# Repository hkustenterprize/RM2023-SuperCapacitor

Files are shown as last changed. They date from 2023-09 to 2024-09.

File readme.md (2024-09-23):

<div align='left'>
    <h1> 本项目续作已开源 </h1>
</div>

请参考
|||
|-|-|
|论坛|[【RM2024超级电容控制器完全开源】 (史上最详细的开源！)香港科技大学ENTERPRIZE战队](https://bbs.robomaster.com/article/54127)|
|GitHub|[hkustenterprize/RM2024-SuperCapacitorController](https://github.com/hkustenterprize/RM2024-SuperCapacitorController)|

<div align='center'>
    <h1>廉价，可靠，高效</h1>
</div>

<div align='center'>
    <h2>RM2023香港科技大学ENTERPRIZE</h2>
</div>

<div align='center'>
    <h1>数控超级电容方案开源</h1>
</div>

> 设计者：蒋益诚
>
> 文档撰写：蒋益诚  戎羿
>
> 香港科技大学ENTERPRIZE战队

# 前言

在RoboMaster机甲大师赛事中，严苛的底盘功率限制规则迫使各参赛队伍从软件和硬件方面研究高效的底盘功率管理方案。早在2018年末，大连交通大学TOE战队，桂林电子科技大学Evolution战队与香港科技大学ENTERPRIZE战队等便相继开源了各具特色的超级电容方案。2020年，官方裁判系统超级电容管理模块与相关限制规则加入，超级电容的使用更加规范化，给各战队带来了不小的挑战。

2021赛季末大连理工凌_BUG战队开源了他们基于双向BUCK-BOOST电路构建的超级电容控制模块，引发广泛关注。我队取其精华，在其基础上进行数次迭代，历经一年时间，完成了低成本，稳定可靠，大功率，高效率的数控超级电容方案。本着技术交流和初心高于胜负的初衷我队现决定将此方案开源，欢迎大家交流学习。

# 方案回顾

自2018年超级电容方案诞生以来，其大致电路方案可分为以下3种

1. 电源 $\Rightarrow$ 恒功率充电模块 $\Rightarrow$ 超级电容 $\Vert$ 底盘电机
2. 电源 $\Rightarrow$ 恒功率充电模块 $\Rightarrow$ 超级电容 $\Rightarrow$ 恒压放电模块 $\Leftrightarrow$ 底盘电机
3. 电源 $\Vert$ 底盘电机 $\Leftrightarrow$ 双向可控功率模块 $\Leftrightarrow$ 超级电容

笔者将基于自身理解对这些方案进行简单优缺点分析

## 电源  $\Rightarrow$  恒功率充电模块  $\Rightarrow$  超级电容 $\Vert$ 底盘电机

本方案直接明了，通过恒功率充电模块对整个底盘的输入功率进行控制，并通过超级电容对能量进行缓存。

该方案主要有以下几个优点：

1. 超级电容直接和底盘电机并联，相当于自带了高效的动能回收机制
2. 理想状态下能够保证在任何时候都无法超功率

在充放电的过程中，底盘电机母线电压是随超级电容电压的波动而波动的，因此该方案存在以下几个显著缺点

1. 如果电容电量过低，会导致底盘电机欠压保护，或工作不正常
2. 电压不稳定，会影响底盘电机的控制，具体可表现为相同参数下电机的输出力矩，转速等存在较大幅度波动。
3. 动能回收时，会有较大的倒灌电流涌入超级电容组，对电容组及其保护板的设计有一定的考验。
4. 在机器人阵亡后，若电容仍有余电，底盘电机可能仍有足够电压继续移动一段时间，若不做处理可能违反规则
5. 模块之间串联，若有模块损坏或异常断电，则机器人底盘直接掉电，无法继续移动

## 电源 $\Rightarrow$ 恒功率充电模块 $\Rightarrow$ 超级电容 $\Rightarrow$ 恒压放电模块 $\Leftrightarrow$ 底盘电机

该方案在上个方案的基础上增加了一个恒压放电模块，以稳定底盘电机母线电压。

因此，该方案有以下几个优点：

1. 与上个方案一样，理想状态下，底盘不会超功率
2. 在电容电量耗尽前，底盘电机的母线电压相对恒定，能够给电机提供良好的工作环境

由于恒压放电模块可能存在的一些特性，该方案可能存在以下几个缺点：

1. 若恒压放电模块为非同步boost/buckboost或者其控制策略不允许电流倒灌（例如其boost半桥上管采用理想二极管策略控制），则该方案完全无法进行动能回收，且在电机急减速时可能瞬间拉高母线电压，有较大风险烧毁电机
2. 在机器人阵亡后，若电容仍有余电，底盘电机可能仍有足够电压继续移动一段时间，若不做处理可能违反规则
3. 与上个方案一样，模块之间串联，若有模块损坏或异常断电，则机器人底盘直接掉电，无法继续移动。且由于恒压放电模块与底盘电机直接相连，工况较为恶劣，对该模块的设计有较大考验。

## 电源 $\Vert$ 底盘电机 $\Leftrightarrow$ 双向可控功率模块 $\Leftrightarrow$ 超级电容

该方案即为本战队本次开源的方案，灵感源自2021赛季大连理工大学凌BUG战队的开源。

在本方案中底盘电机直接连接到电源，超级电容和一个双向可控功率模块共同构成一个可控的功率补偿系统，凭借高速的功率闭环控制动态对底盘功率进行削峰填谷，从而实现超级电容的能量缓冲。

为便于理解，在此举例。

假设底盘功率限制为60W，电池电压为20V，超级电容处于半充满状态。

若此时底盘电机电流为2A，即底盘电机功率为40W，则双向可控功率模块将使用1A电流对超级电容充电，即充电功率为20W。将多余功率缓存在超级电容中。

若此时底盘电机电流为5A，即底盘电机功率为100W，则双向可控功率模块将使用2A电流对超级电容进行放电，此时放电功率为40W。利用超级电容中的能量补偿底盘功率。

若此时底盘电机电流为-2A，即底盘电机功率为-40W，则双向可控功率模块将使用5A电流对超级电容进行充电，此时充电功率为100W。即动能回收的过程。

该方案具有如下几个主要优点：

1. 并联接入底盘电机母线，即使系统工作异常，只需要及时切断电路（关断MOS管/保险丝熔断等），底盘任可继续正常工作。
2. 无论电容剩余能量如何，底盘电机的母线电压都能保持相对稳定，约等于电源电压，能够给电机提供良好的工作环境。
3. 可以主动限制动能回收的电流，允许部分浪涌电流倒灌回电池，防止损坏超级电容组。
4. 通过简单的代码逻辑，可在底盘电源切断时立即关断系统输出，在机器人阵亡后保存电容能量，同时避免违反规则。

该方案的显著缺点如下：

1. 采用数控方案，对嵌入式程序设计，控制系统设计要求较高，稍有不慎即可能损伤硬件。（我们调试时曾不慎将输出电压升至100V以上）
2. 采用并联方式被动补偿功率，若底盘电控不加以合理限制，仍有超功率风险。

显然，在参赛队伍硬件实力足够的前提下，第三种方案相较于前两种有极大优势。我们本次开源的方案即基于第三种。

# 电学原理

## 升压与降压

首先回顾经典的升压电路与降压电路。为方便理解，假设此处所有DC-DC电路均工作在CCM（连续导通）模式下，MOSFET（场效应管）为理想MOSFET，忽略死区时间， $R_{DSon}$ 等。

- Buck降压。下图左侧为非同步Buck电路，肖特基二极管起到为电感续流的作用。右侧为同步Buck电路，用MOSFET替代了二极管，带来了更低的压降与更灵活的控制。同步Buck电路中，CCM模式下，MOSFET经过**控制**，能够在电流正向的时候导通、反向的时候断开，实现了二极管的功能。

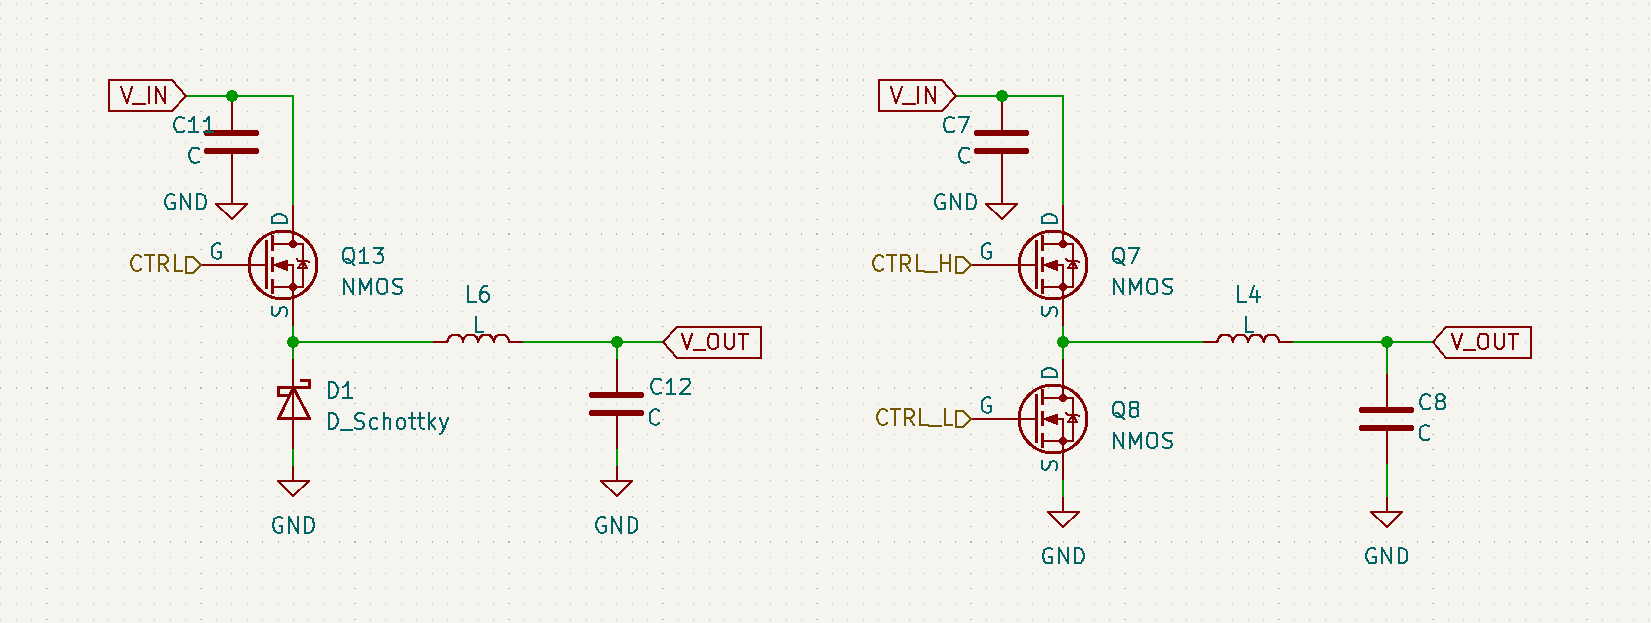
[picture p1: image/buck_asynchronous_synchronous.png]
buck_asynchronous_synchronous
    通过伏秒平衡定律可推导Buck电路在CCM模式下的输入输出电压关系 $\frac{V_{out}}{V_{in}}=D$ ，其中 ${V_{out}}$ 为输出电压， $V_{in}$ 为输入电压， $D$ 为上管导通时间占整个PWM周期的占空比。

- Boost升压。下图左侧为非同步Boost电路，MOSFET对地导通时为电感充能，二极管在此处起到续流和防倒灌作用。右侧为同步Boost电路。用MOSFET替代二极管，在适当的控制下实现了二极管的功能。

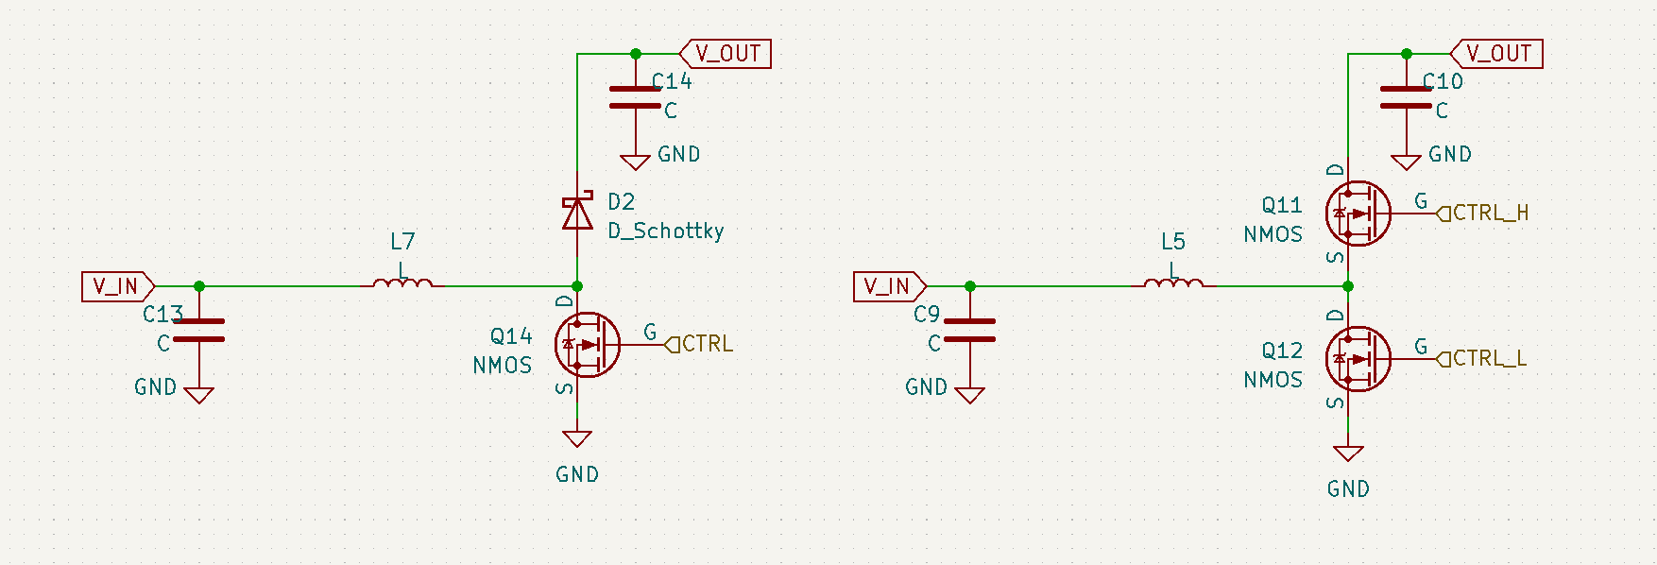
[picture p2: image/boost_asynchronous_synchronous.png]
boost_asynchronous_synchronous
    通过伏秒平衡定律可推导Boost电路在CCM模式下的输入输出电压关系 $\frac{V_{out}}{V_{in}}=\frac{1}{D}$ ，其中 ${V_{out}}$ 为输出电压， $V_{in}$ 为输入电压， $D$ 为上管导通时间占整个PWM周期的占空比（注意是上管）。

  受限于篇幅，在此省略伏秒平衡定律的具体推导过程。

## 双向升降压

同样的，假设一切条件全部理想，将Buck电路的前半段与Boost电路的后半段相连，我们可得到如下的四开关双向Buck-Boost电路。观察可见，此电路为对称结构。

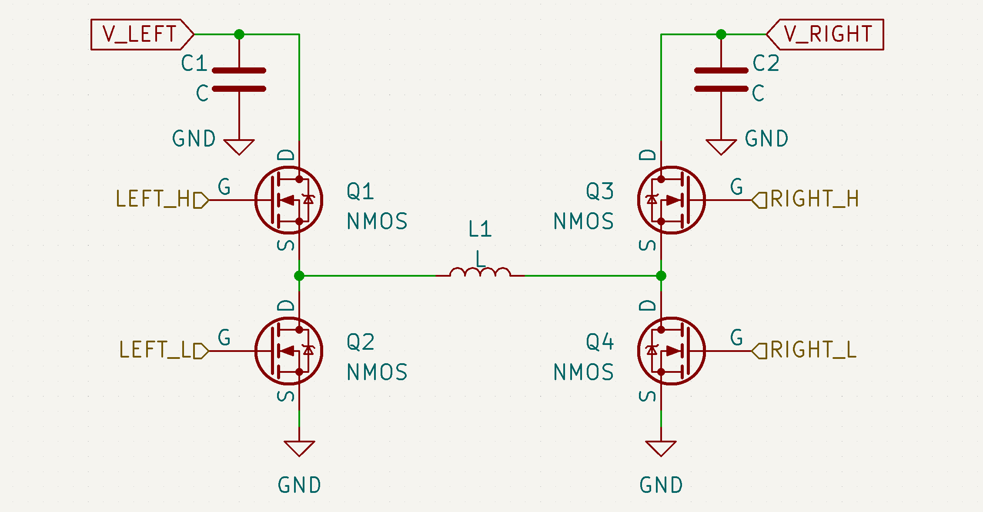
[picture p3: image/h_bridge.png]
image-principle-1


### 假设电流从左往右流动

- 若将RIGHT_H常导通，RIGHT_L常断开，而LEFT_H和LEFT_L继续使用如上的Buck电路控制策略，则等效电路图如下图。这就是完全等效于Buck的拓扑，此时可将电路看作同步Buck，可实现将左侧电降压后提供给右侧。

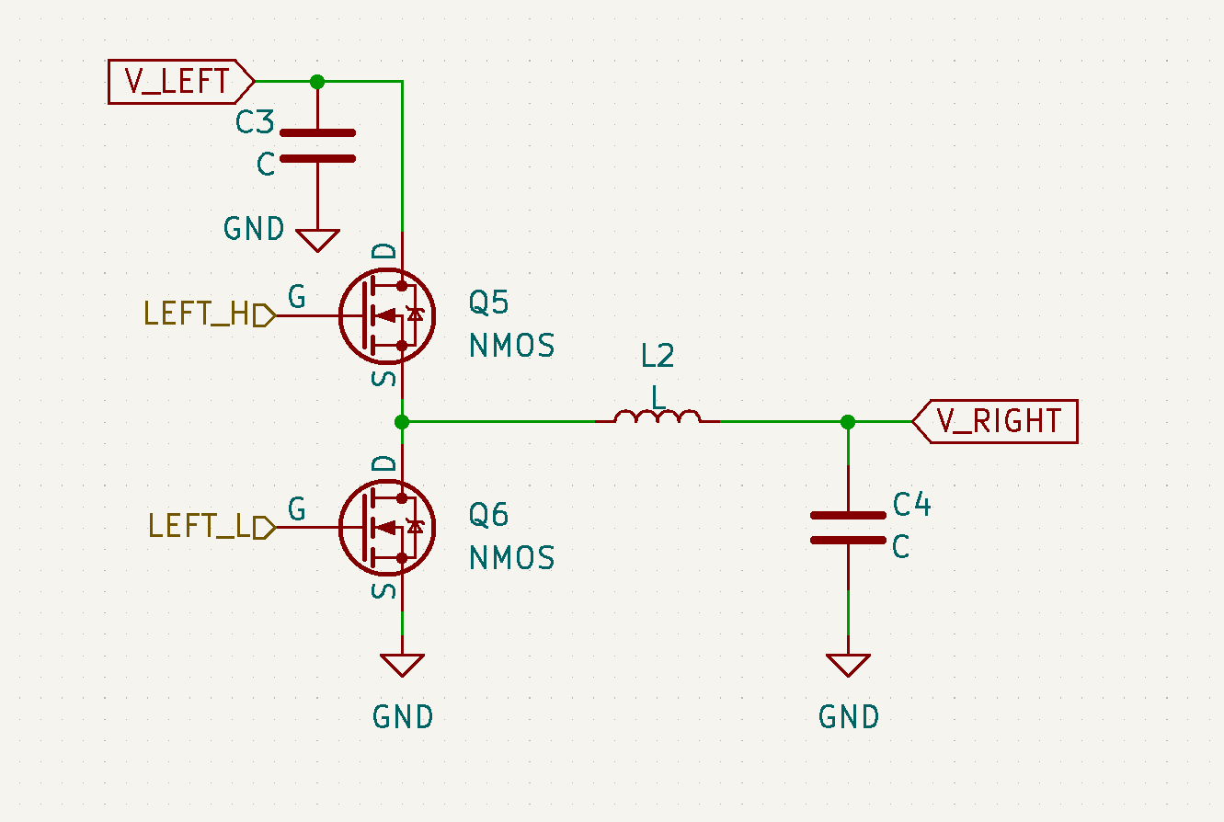
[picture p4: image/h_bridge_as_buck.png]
  
- 若将LEFT_H常导通，LEFT_L常断开，而RIGHT_H和RIGHT_L继续使用如上的Boost电路控制策略，则等效电路如下图。这就是Boost的拓扑，此时将电路看作同步Boost即可实现将左侧电升压后提供给右侧。

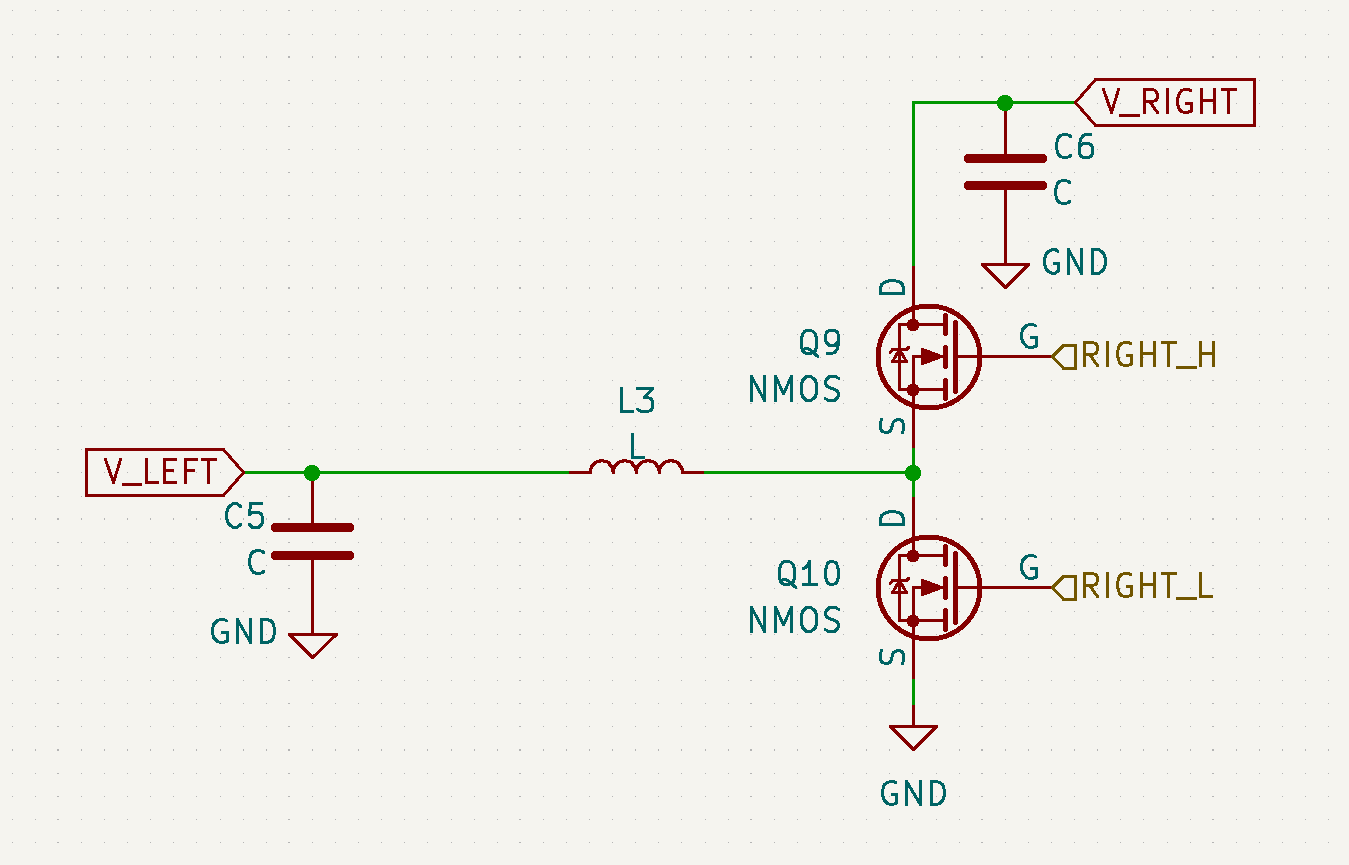
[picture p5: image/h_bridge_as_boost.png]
  
- 第三种情况是需要的左电压与右电压相近。此时实际应用中由于最大占空比以及死区时间等限制，很难单独使用Buck或者Boost拓扑生成所需电压比。于是考虑用Buck控制策略控制左半桥，用Boost控制策略控制右半桥，此即为buck-boost电路。在任意时刻（瞬时），电路可视为Buck电路或Boost电路。（此处省略了一些细节，如为了防止两边的下管同时导通，左右两边的上管占空比应相互制约，同时相位也应错开）此时，无论是使用叠加原理还是通过伏秒平衡定律，我们都可以得到如下结果 $\frac{V_{left}}{V_{right}}=\frac{D_{right}}{D_{left}}$ ，其中， $D_{left}$ 为左侧上管占空比， $D_{right}$ 为右侧上管占空比。

### 假设电流从右往左流动

由于电路完全对称，显然，仅需将Buck与Boost颠倒过来，即可实现与上述完全相同的效果，在此不做过多赘述。

经过同样的推导，我们仍然得到此结果 $\frac{V_{left}}{V_{right}}=\frac{D_{right}}{D_{left}}$ 。

### 总结

在控制这个四开关双向Buck-Boost电路时，实际上**不需要区分电路到底是Buck还是Boost**，也不需要关注电流的流向等，只需给予两个半桥合适的占空比，即可获得想要的左右电压之比。

这种不对电流流向做限制，强制上下管交替导通的控制方式被称为FPWM（强制脉宽调制）模式。由于实现此控制模式的硬件较为简单，本设计采用此控制模式进行控制。

注意：Buck与Boost的互相转换只在 *同步Buck/同步Boost* 中起作用。

## 电流控制

通过以上分析，我们现可构建一个四开关Buck-Boost双向升降压电路。

在RoboMaster以及大多数其他应用场景中。电路中的负载更偏向于阻性，即电压差越大，电流越大，根据这一特点，我们通过控制左右两侧的电压之比进而对左右两侧的平均电流进行控制。

此处举一个例子便于理解。假设左侧为电源，右侧为负载，根据以上分析，我们可推导出右侧电压越大，输出电流越大，右侧电压越小，输出电流越小。此时若输出电流大于目标电流，则我们通过改变左右两侧占空比，控制左右两侧电压之比增大，则右侧电压降低，输出电流也相应减小。若输出电流小于目标电流，则控制占空比减小，右侧电压升高，输出电流增大。当右侧为电压源时，只需反转控制逻辑，即可实现一样的控制效果。在RoboMaster超级电容的应用中，左侧和右侧均可作为负载或电源，当给超级电容充电时，超级电容侧为负载，当超级电容放电时，超级电容侧为电源。

在上述例子中，基于电流反馈控制占空比变化的方式有很多种，在本方案中，我们使用ADC对转换后的电流进行读取，之后使用PID计算所需占空比进行输出，从而实现电流闭环控制。

# 控制模块技术特点

## 实物图

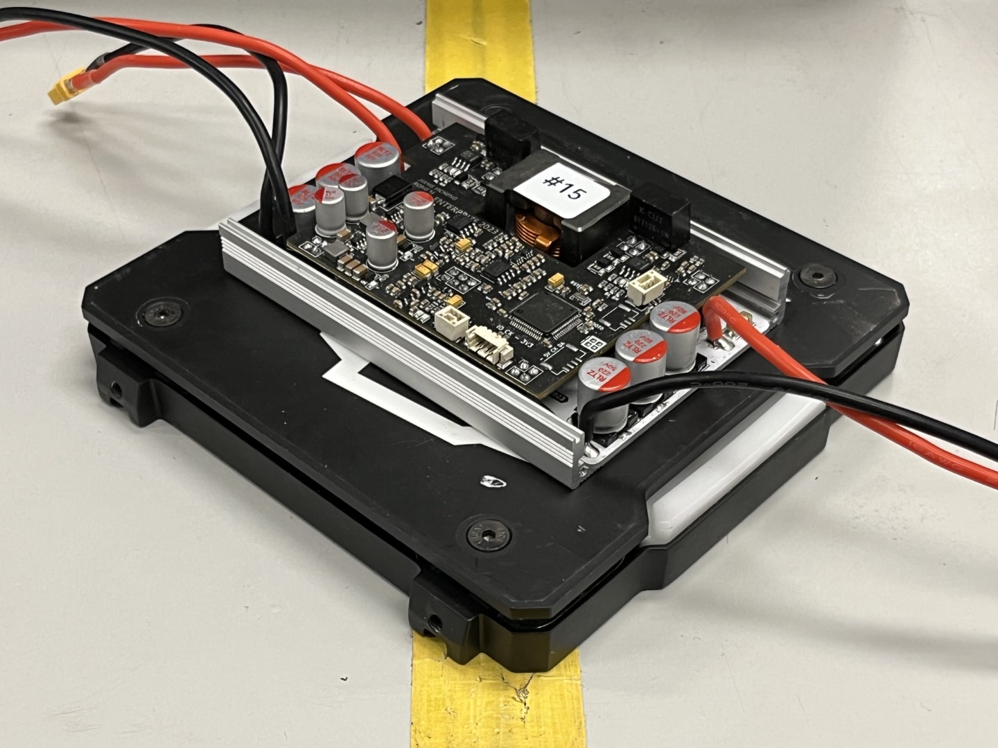
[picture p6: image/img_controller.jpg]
img_controller


## 硬件

- 上下板组合

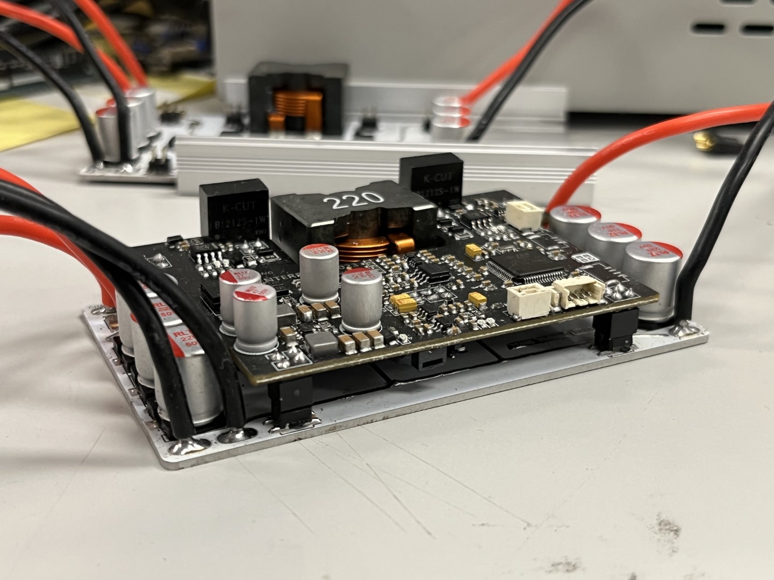
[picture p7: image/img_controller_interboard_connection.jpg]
img_controller_interboard_connection
  

  - 上板为FR4四层板，负责控制与驱动，带有MCU、信号调理电路、MOSFET栅极驱动、电流感应放大器电路、CAN通信电路，以及相应的辅助供电电路等。
  - 下板负责功率部分，为铝基板。带有保险丝、MOSFET、扁线功率电感、固态电容以及采样电阻等，利用铝基板加强散热，使得超级电容控制模块可以持续输出15A以上大电流而保持凉爽。
  - 上下板通过矮排针排母连接。模块化的设计方便快速更换组件，也方便维修上板或下板。
  - 功率线路从下板直接引出，导线直接焊接在焊盘上，大电流不需要经过上下板连接处，因此可以使用一般的排针排母进行简单的连接。

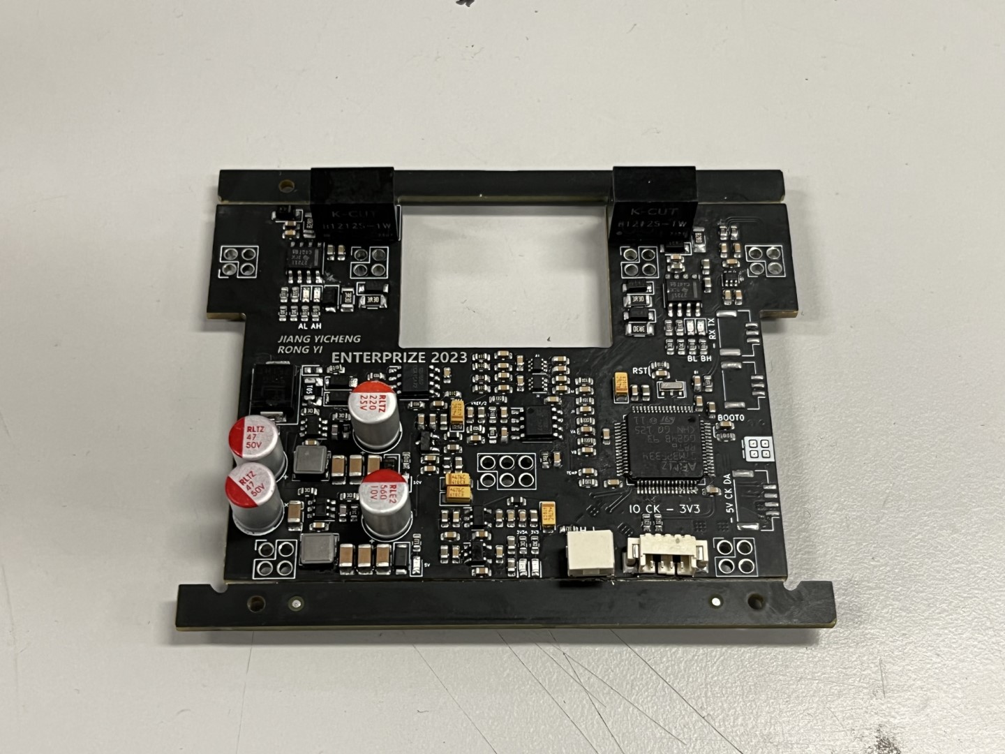
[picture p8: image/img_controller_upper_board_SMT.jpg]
img_controller_upper_board_SMT
    

    *嘉立创贴片+手焊后的电容控制器上板*

- 电感值计算

  本方案设计最大电流为15A，考虑3A的纹波电流，假设电路足够理想，忽略详细的电感取值计算公式推导过程。
  -  Buck模式下工作时，电感取值应满足 $L_{Buck}>{(\frac{V_{out}}{\Delta{I}\cdot{f}} \cdot (1 - D))}_ {max}$ 。其中， $V_{out}$ 为输出电压， $\Delta{I}$ 为纹波电流， $f$ 为开关频率， $D$ 为上管占空比。
     分析可得，当输入电压最大(此时超级电容组作为电源输出，最大电压29.15V)，占空比为0.5时上式右侧取得最大值 ${\frac{29.15 \cdot 0.5}{3 \cdot 288000}} \cdot (1 - 0.5) = 8.434 uH$ 。因此，在Buck模式下，电感取值不应小于8.434uH。
  -  Boost模式下工作时，电流流向反转，将上述公式中的 $V_{out}$ 输出电压换为 $V_{in}$ 输入电压，即得到 $L_{Boost}>{(\frac{V_{in}}{\Delta{I}\cdot{f}} \cdot (1 - D))}_ {max}$ 其中， $V_{in}$ 为输入电压， $\Delta{I}$ 为纹波电流， $f$ 为开关频率， $D$ 为上管占空比（注意是上管）。
      分析可得，当输出电压最大(此时超级电容正好被充满电，最大电压29.15V)，占空比为0.5时上式右侧取得最大值 ${\frac{29.15 \cdot 0.5}{3 \cdot 288000}} \cdot (1 - 0.5) = 8.434 uH$ 。因此，在Boost模式下，电感取值不应小于8.434uH。
  -  在不超过饱和电流的前提下，电感取值越大，纹波电流越小，留出一定余量，实际中使用饱和电流为21A，温升电流为30A的15uH的扁线电感。(实际上测试使用22uH饱和电流为14A，温升电流为30A的电感也可以工作，但出现了大电流下纹波明显增大的情况，保险起见最终选用了15uH电感，可考虑降低到10uH，选择更小的体积)

- 电容值计算

  考虑100mV的输出电压纹波，其余参数与计算电感时相同，假设电路足够理想，采用合适的近似方式，忽略详细的电容取值计算公式推导过程。
  - Buck模式下工作时，电容取值应满足 $C_{Buck}>\frac{\Delta{I}}{8\cdot{f}\cdot{\Delta{V_{out}}}}$ 。其中， $V_{out}$ 为输出电压， $\Delta{I}$ 为纹波电流， $f$ 为开关频率， ${\Delta{V_{out}}}$ 为输出电压纹波。
  计算可得，Buck模式下电容取值应大于 $\frac{3}{8\cdot{288000}\cdot{0.1}} = 13.02 uF$ 。因此，在Buck模式下，电容取值不应小于13.02uF。
  - Boost模式下工作时，电容取值应满足 $C_{Boost}>{\frac{I_{out}\cdot{(1-D)}}{{f}\cdot{\Delta{V_{out}}}}}_ {max}$ 。 其中， $I_{out}$ 为输出电流， $D$ 为上管占空比， $f$ 为开关频率， ${\Delta{V_{out}}}$ 为输出电压纹波。
  分析可得，当输出电流最大(15A)，上管占空比最小(软件限制为0.1)时右侧取得最大值 $\frac{15\cdot{(1-0.1)}}{{288000}\cdot{0.1}} = 468.75uF$ 因此，在Boost模式下，电容取值不应小于468.75uF。
  - 理想情况下，电容取值越大，纹波电压越小，留出一定余量，并考虑到ESR影响，实际应用中，我们使用4个耐压为100V，额定容量为10uF的陶瓷电容与3个耐压50V，容量为220uF的固态电容并联，总电容值约为 $4 \cdot 6 + 3 \cdot 220 = 684 uF$ (考虑陶瓷电容的直流偏压特性)。

- MOSFET驱动方案

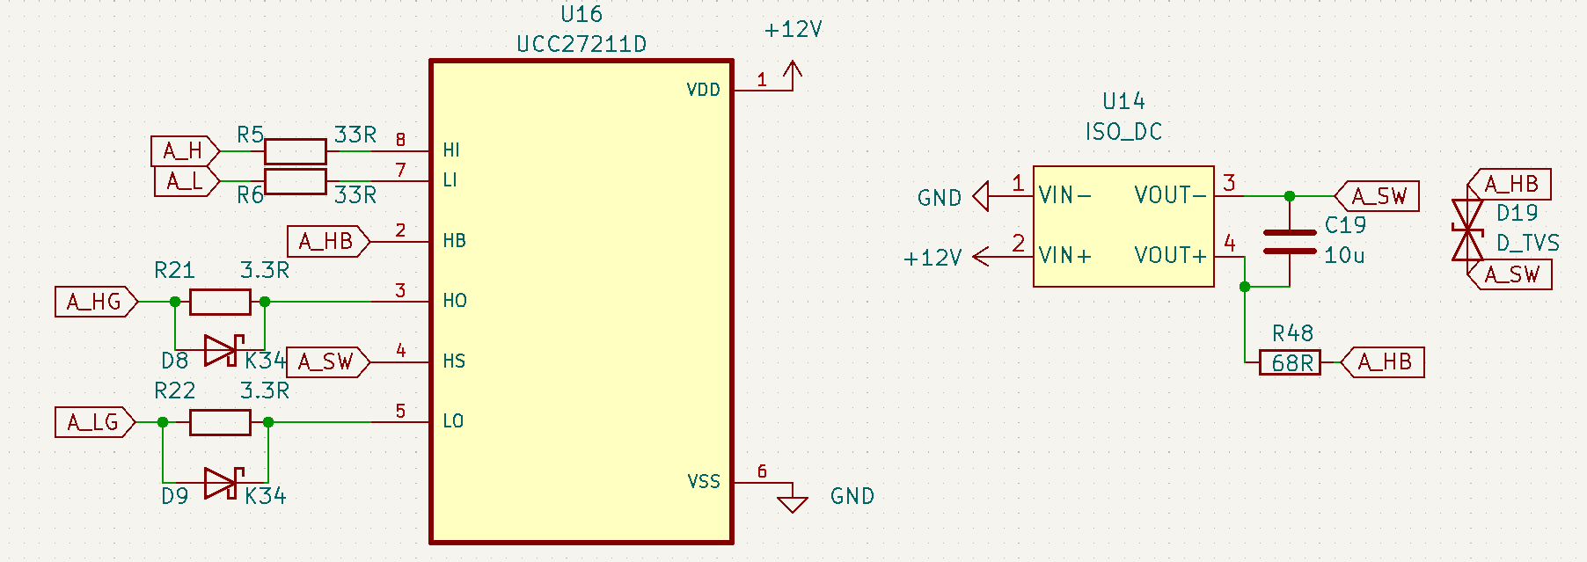
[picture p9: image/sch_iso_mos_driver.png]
sch_iso_mos_driver
  MOS驱动为UCC27211。采用隔离供电取代UCC27211的自举电容，从而能够实现100%占空比常开上管，显著提高单边Buck/单边Boost的转换效率

  - 通常，UCC27211使用一个自举电容串联在引脚HB(BootStrap)与HS(Switching)之间，芯片自带自举电路，通过浮空自举电容来打开上管。这种做法体积小，但是自举电容需要充电，需要定期导通下管为电容充电来弥补自举电路及栅极驱动等的漏电电流，做不到100%占空比。因此实际上总是工作在buck-boost模式下。由于两侧MOSFET都需要不断开关，损失了一些效率。
  - 此处使用12V->12V DCDC的隔离供电模块。因为此隔离供电模块为开环控制，输出电压极不稳定，且纹波极大，很容易炸毁栅极造成严重后果，所以此处使用RC滤波，并加入TVS(SMF10A)来钳位，保护上管不被高电压击穿。
  
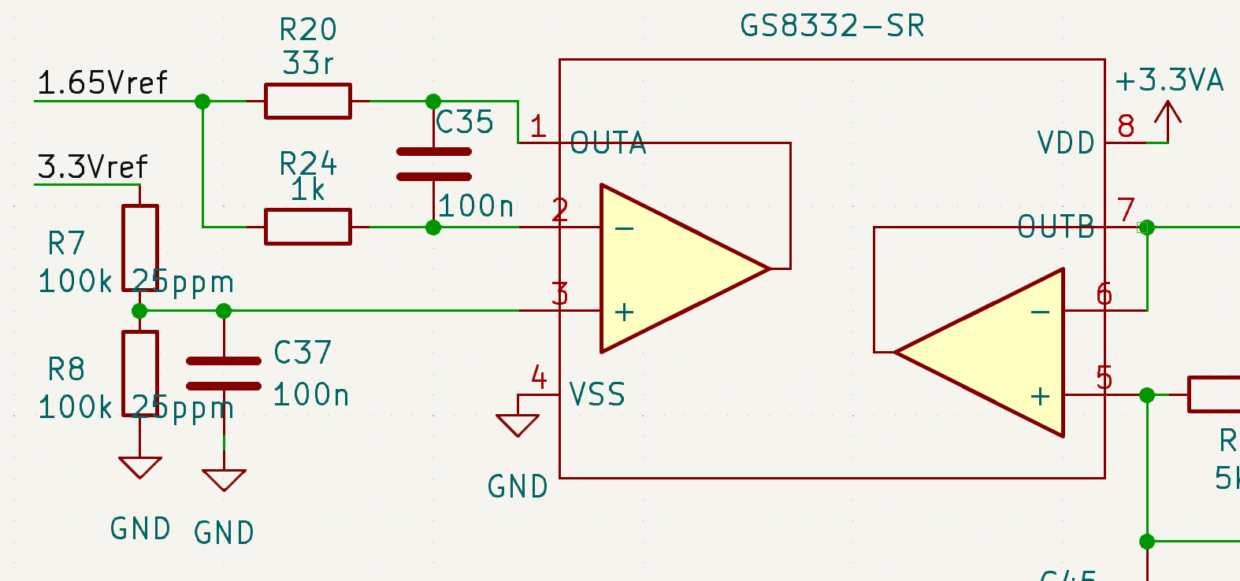
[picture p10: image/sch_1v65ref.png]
sch_1v65ref
- 电流感应放大器所需的1.65V参考电压源由运放电路使用3.3V分压产生。使用阻容网络进行相位补偿，防止驱动容性负载时环路不稳定产生震荡。

- 电流感应放大选择使用INA186差分放大器芯片

  在一众开源方案中，较多使用 INA240 作为电流感应放大器。然而INA240的价格与供应不如人意，在此背景下相关开发人员使用了 INA282 进行替代。但是，INA282 的封装为 SOIC-8，体积大，layout 占用过多空间。其次INA282 最小增益倍数为 50 倍，增益带宽较低，实际测试过程中出现信号失真的问题。 因此经过反复比对选型，最终使用了另一款电流感应放大器 INA186，选择其最低增益倍数的版本INA186A1。这款放大器体积小，支持双向电流采样，带宽也能达到标准，耐压能够支持高位采样的需求。但在实际测试过程中发现其对于共模干扰的抑制能力非常差，极易受到开关信号干扰。

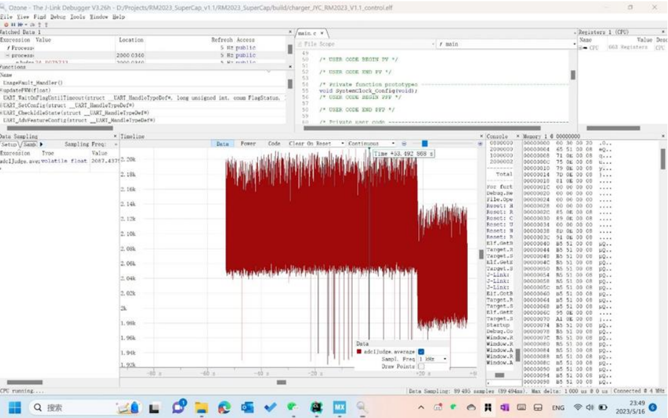
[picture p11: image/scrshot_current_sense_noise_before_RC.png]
scrshot_current_sense_noise_before_RC
  

  为应对此干扰，在实际电路设计中加入了 RC 滤波电路，截止频率13kHz，实测能够有效过滤共模干扰和电源本身的噪音。

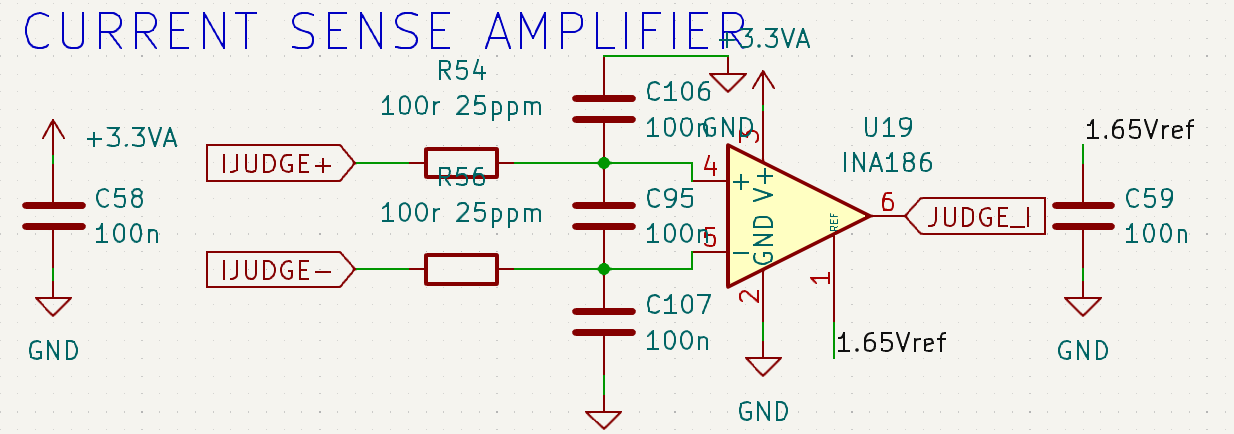
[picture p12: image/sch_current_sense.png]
sch_current_sense
  

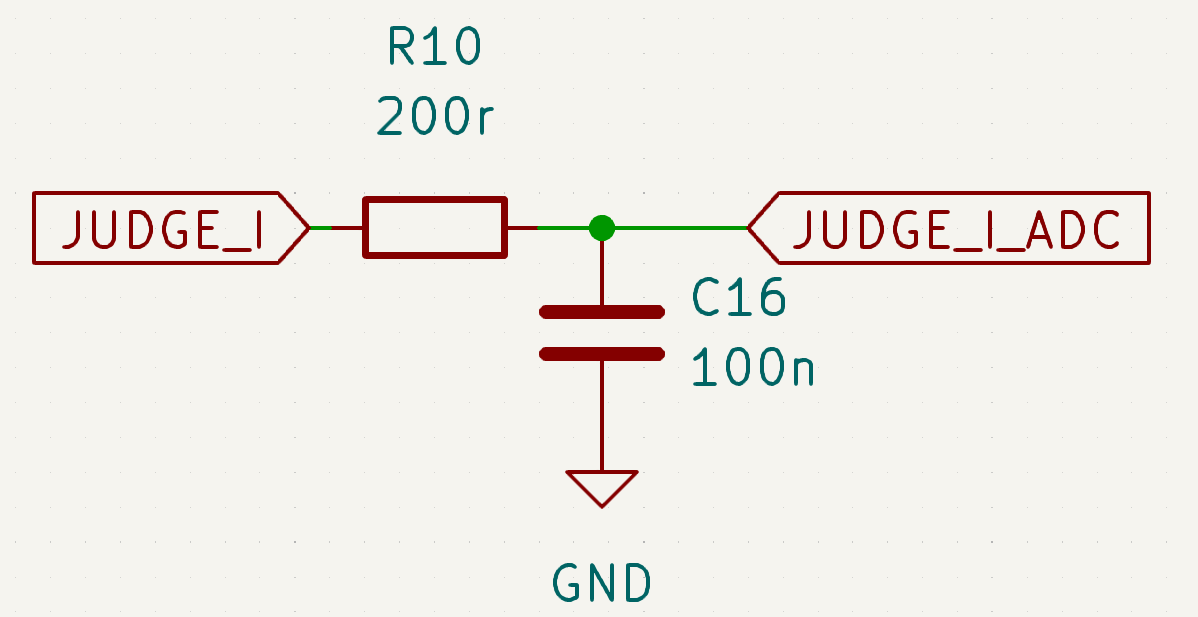
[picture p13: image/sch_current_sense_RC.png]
sch_current_sense_RC
  

  - INA186耐压高达42V，可以实现高位采样
  - 相比常用的INA240，INA186价格优势非常大，能显著节省整体成本
  - INA186的有效带宽20kHz，对于pwm频率约288khz的应用已经足够
  
- 使用全包裹铝壳，兼顾散热与保护

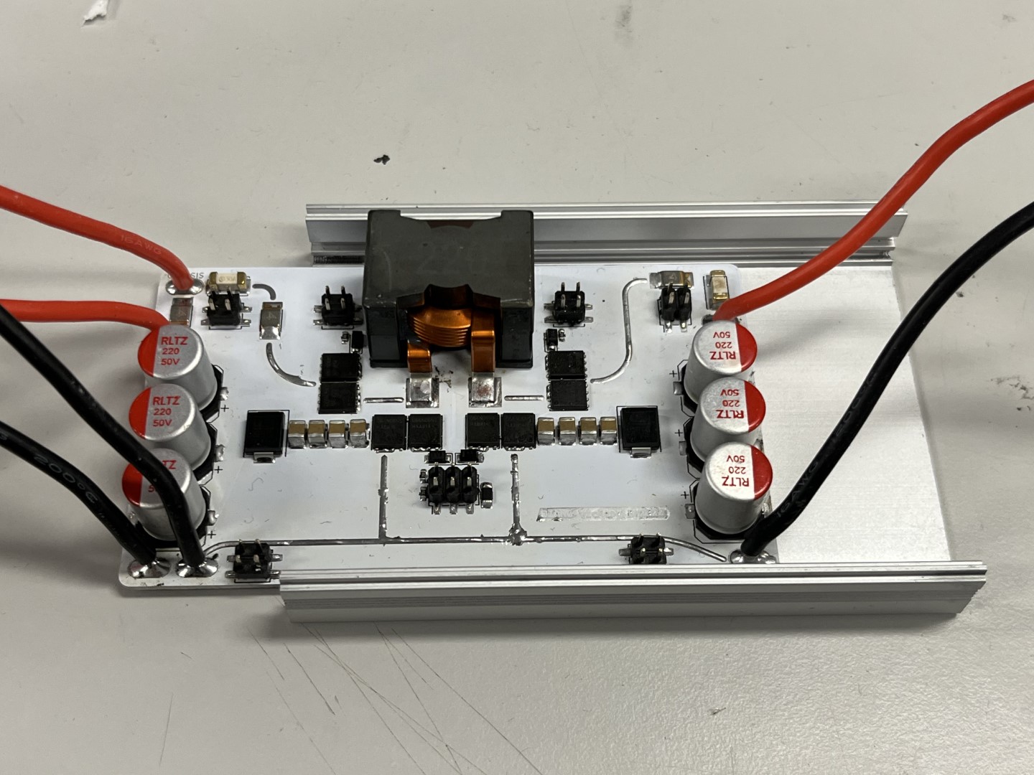
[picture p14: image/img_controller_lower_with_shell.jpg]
img_controller_lower_with_shell
  

  *下板用导热胶贴在铝壳上，提高散热效果*

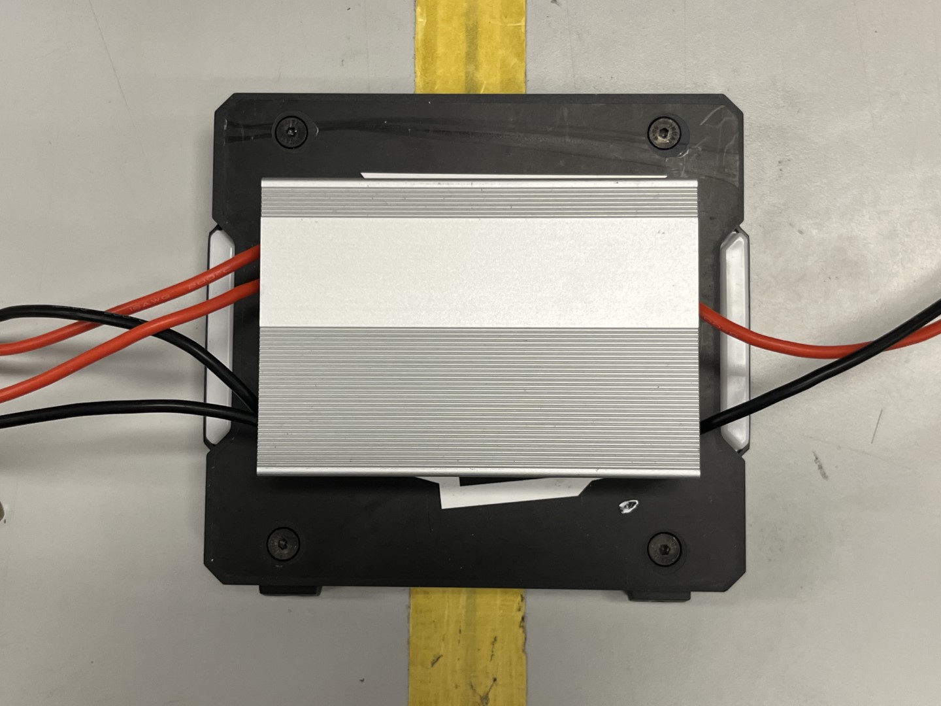
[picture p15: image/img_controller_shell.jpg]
img_controller_shell
  

  *大小对比（与装甲板相比）*

  - 此超级电容控制模块效率最高约为97.8%。在处理大电流的情况下，不可避免地产生能量损耗，因而需要将热量导至铝制部件来散热。
  - 对于模块的外壳，我们采用工业化生产的全包裹铝壳。它既充当了散热组件，同时也能屏蔽电磁，防止超级电容控制板的EMI影响敏感部件例如RFID、UWB等。
  - 全包裹铝壳同样有很好的结构强度，在恶劣的使用情况例如翻车、剧烈冲撞时可以有效保护内部功率电路。密封的设计也可以防止异物进入，例如打磨产生的铝屑，碳粉，以及香港恶劣潮湿气候常见的水雾等。这对于超级电容这种大功率的模块的稳定性和安全性而言非常重要。

## MCU外设使用

### MCU选择

- 四开关Buck-Boost电路中，开关频率越高，则需要的电感大小就越小，其体积也就越小。
- 我们使用STM32芯片的Timer外设输出开关控制的PWM信号。为了实现精准的占空比控制，时钟周期不能太小；而普通Timer外设的频率一般仅有几十上百兆赫兹，开关频率高与时钟周期大无法同时实现。为实现精准控制，我们选用HRTim即高分辨率定时器外设，部分带有倍频功能，如STM32F334的HRTIM可以倍频至4.9GHz，实现288KHz的PWM频率同时，也有16000的分辨度。
- 带有倍频功能HRTim的MCU中，能轻松买到的有STM32F334系列与STM32G474等。它们HRTim的功能几乎完全一样，而STM32G474比STM32F334有更高的主频与更先进的外设。然而，STM32G474在成本上有很大劣势，且大部分多出来的外设在超级电容上并不会有应用；同时，我们的代码在经过优化之后已经可以在STM32F334上以60%的内核占用实现36kHz频率的闭环，受限于电流采样带宽与开关频率，此闭环频率已足够应对RoboMaster赛场上复杂的工况。因而我们最终选择了简单实惠的STM32F334作为此项目的MCU。

### 外设配置

#### HRTIM Master Clock

- 调整倍频与周期，使PWM频率为288kHz

#### HRTIM Timer A

- 负责A半桥MOS的开关信号
- 负责触发A侧的ADC采样

#### HRTIM Timer B

- 同理

#### 死区控制

* 同一边半桥的上下管绝对不能同时打开，否则电流回直接通过上下管对地短路，造成严重后果。同时，MOSFET导通时需要给栅极电容充电，需要一个几到几十纳秒的过程。因此，我们打开了HRTimer外设的Dead Time功能，从外设层面防止上下管对穿。本设计中我们为了防止MOSFET开关过快导致振铃，配置的上升下降时间较大，死区时间通过测试得出：8分频下Rising与Falling各约110（此值仅为参考，需根据实际情况微调）。
* 若死区时间太大，则在死区时间的后半段，由于MOS管没有及时开启，会有较大电流从MOS管的寄生二极管流过，降低效率并增加过热烧毁的风险；若死区时间太小，则前一个MOS还没有完全关断的时后一个就已经正在打开了，此时容易发生上下管对穿的情况，会严重发热，烧毁MOS管。
* 实际调节死区时间时，可使用具有恒压恒流功能的可调电源给数控超级电容模块进行供电，逐步调小死区，当可调电源突然出现CC（恒电流）模式时，代表死区时间过小，上下管之间已经短路，在此时的死区时间基础上添加一个安全冗余即为合适的死区时间。为了防止用户代码层面对死区进行错误修改导致灾难性后果，可配置死区相应寄存器进入只读模式，防止配置成功后在代码正常运行中被二次修改。

====

* *同时*，左侧与右侧半桥的下管也不能同时打开，否则就相当于电感两端经过GND短路，使其储存的电磁能瞬间转化成热能。在我们的实际应用中，我们通过错开TimerA与TimerB的相位180°，并限制Buck-Boost模式下TimerA与TimerB的上管占空比均不得小于50%来实现这一功能。

#### HRTIM ADC Trigger

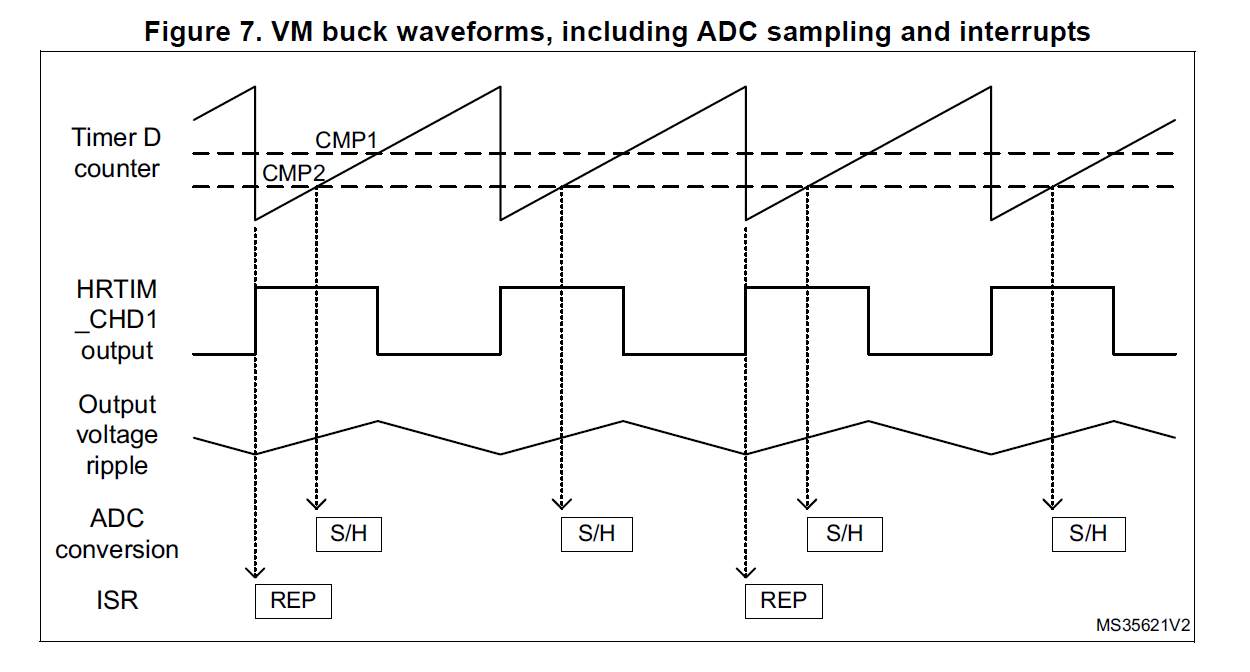
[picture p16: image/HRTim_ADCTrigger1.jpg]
HRTim_ADC_Trigger1


在电路实际工作过程中，MOSFET的开关会给电压带来纹波进而产生电流纹波。为防止MOSFET开关瞬间引入电流采样共模干扰，或产生的电流纹波影响采样，电流采样的时机应当正好处于对应侧上管PWM波形的中点，此时瞬时电流值等于平均电流值，瞬时电压值等于平均电压值。我们通过如下配置来实现这一功能。

- TimA Compare2 -> ADC Trigger 1
- TimB Compare2 -> ADC Trigger 3

#### ADC1

- CH1 -> V_SENSE_A（左侧电压采样）
- CH2 -> I_SENSE_JUDGE（裁判系统电流采样）
- CH3 -> I_SENSE_A（左侧电流采样）
- 触发事件：HRTIM Trigger 1 Event

#### ADC2

- CH7 -> I_SENSE_B（右侧电流采样）
- CH8 -> THERMAL_SENSE（温度采样）
- CH9 -> V_SENSE_B（右侧电压采样）
- 触发事件：HRTIM Trigger 3 Event

#### ADC读数校准

- 由于硬件上的误差如电阻阻值、运放芯片的体质、焊接工艺等区别，采得的ADC读数会有误差。我们对每一个焊接后的硬件都进行校准，并将校准数据写入宏，在编译期控制。
- 将读数误差视为线性的，则每一个数据有对应的bias与gain。经过校准之后，不同控制板的电流电压读数几乎一致。
- 将硬件ID写入Bytecode，防止烧错代码（编译时flag写错）。

## 软件

### 充放电控制策略

- 采用多环串联PID：最外环为裁判系统功率闭环，而后功率闭环，最后同时闭环电压与电流。

  - 功率、电压和电流闭环速度为 36kHz，能量闭环速度为 10Hz，通讯频率为 1kHz。
  - 为了实现软启动与无扰切换，我们在电容关断输出不开关 MOS 管时，时刻保持内部 HRTIM 的 PWM 占空比等于两侧电压之比，这使得模块启动的瞬间不会产生巨大的冲击电流。
  - 在具体输出 PID 结果时，我们采用了电压前馈控制，PID 结果在两侧电压之比上进行补偿，有效提升了瞬态响应与控制的线性度。

### VBToVA -> 两半桥PWM占空比

经过PID运算后得出 $V_BToV_A$ ，既理想情况下两侧电压之比。

1. $V_BToV_A < 0.8$，则视作从**从左往右的Buck模式**。 此时右侧上管常开(100% Duty Cycle)，左侧作为同步Buck，则左侧上管的占空比即 $V_BToV_A$ 。
2. $V_BToV_A > 1.25$，则视作**从左往右的Boost模式**。 此时左侧上管常开，右侧为同步Boost，右侧上管的占空比为 $\frac{1}{V_BToV_A}$ 。
3. $V_BToV_A\in[0.8, 1.25]$ ，则Buck或者Boost难以实现这样的升降压。于是采用**Buck-Boost模式**。 此时左侧上管占空比 $\frac{4}{9}\cdot(1+x)$ ，右侧上管占空比 $\frac{4}{9}\cdot(1 + \frac{1}{x}) $，这个值满足 $\frac{D_A}{D_B} = \frac{V_B}{V_A}$ ，且保证两边占空比的变化是连续的，可实现无缝衔接，防止占空比突变导致的控制不稳定。

### 通讯与底盘功率控制策略

* 为保持通讯稳定性，使用CAN协议进行通讯，硬件上直接将CAN总线接入底盘电机所在的CAN总线，保证能读到电机即能读到电容反馈。
* 每毫秒向底盘控制板反馈电容剩余能量、底盘瞬时功率、瞬间最大输出功率等信息，辅助底盘控制板上的功率控制代码进行底盘电机功率控制。
* 每100毫秒接收一次来自底盘控制板的回报信息，包括来自裁判系统的剩余能量信息，来自裁判系统的功率限制信息，电容模式控制信息等。利用此信息对功率控制的误差进行修正（能量闭环），并在必要时刻提升瞬态响应（回家后功率瞬间翻倍）。

### 故障处理

该模块为了保障安全性，设计了数种故障模式，排查了几乎所有会导致灾难性后果的情况。此模块工作之稳定，在整个RoboMaster2023的赛季开发中，扛住了数次接错线、电容组极性接反、输出短路、信号调理部分电路短路等严重故障，至今未出现任何损坏烧毁的案例。

- 过压保护

  - 模块会检测电容与底盘的电压，若电压过高，为防止模块本身工作异常导致毁灭性后果，会自动进入锁定状态。
  - 模块认为，任何时刻，AB 电压均不得大于 31V。若检测到超过 31V 的电压，模块会立即进入锁定状态。
  - 刹车制动时，底盘电机会将能量倒灌回裁判系统，这些能量的部分会被模块吸收，但当电容充满或倒灌能量过大，电容无力吸收这部分能量，会导致底盘电压升高。为保护底盘电机，防止因模块本身异常导致底盘电机烧毁，模块会检测超过 27V 的底盘电压，若符合一定逻辑，则进入锁定状态，任由能量倒灌回电池。

  对于底盘输出电压有以下检测逻辑:

  1. 若底盘电压持续大于 27V 但小于 28V 超过 300ms，则进入过压状态。
  2. 若底盘电压持续大于 28V 但小于 29V 超过 60ms，则进入过压状态。
  3. 若底盘电压持续大于 29V 但小于 30V 超过 12ms，则进入过压状态。
  4. 若底盘电压持续大于 30V 但小于 31V 超过 3ms，则进入过压状态。
  5. 当 A 相电压小于 27V，B 相电压小于 31V，过压锁定自动解除，模块自动尝试重新启动。
- Buck-Boost 故障

  - 由于校准误差，代码跑飞或逻辑bug，局部短路等问题，模块可能会出现升降压部分工作异常的情况，当检测到此部分电路工作异常，模块进入锁定状态，关断输出，且不会自动尝试重新启动，需要用户手动重置。
- 短路

  - 当模块检测到短路，会立即关断输出，短路状态立即解除，之后模块会尝试重新启动输出。 若短时间内连续检测到多次检测到短路故障，模块认为硬件损坏，不再尝试重新启动输出，需要用户手动重置。
- 高温

  - 当模块检测到温度过高，会进入高温保护状态，关断输出。 待温度下降后自动恢复，重新启动输出。
- 裁判系统供电丢失

  - 当模块检测到裁判系统供电丢失时（通常为机器人阵亡），自动关断输出。 待裁判系统供电恢复时，自动尝试重新启动。
- 电容组故障

  - 当模块检测到超级电容故障，模块进入锁定状态，关断输出，且不会自动尝试重新启动，需要用户手动重置。
  - 检测超级电容故障的逻辑如下：
  - 1. 当超级电容电压变化达到一定阈值时，若充入超级电容的电荷量过低，认为与超级电容之间的连线断开。 （有效电容值过低）
    2. 当充入超级电容的电荷量达到一定阈值时，若超级电容的电压变化过小，认为超级电容局部短路，过充，或漏电。
    3. 为防止电荷量累计漂移误差，若未处于故障状态，每隔一段时间会重置故障检测。
- 超级电容控制器配合新电容组可以判断正负极性错误

  - 如果正负极接反，电容处于空电状态，会判定为短路，发出短促的嘟嘟嘟提示音。
  - 如果电容正负极接反，且电容处于满电状态插入，将会剧烈打火并烧毁电容控制器下板上对应的TVS或保险丝，从而保护控制部分电路与MOS管。此后无论是否接电容，再次给超级电容控制器通电都会发出短促的嘟嘟嘟提示音，需要更换超级电容控制器上的TVS与保险丝

  故障提示及处理

1. 当超级电容进入任何故障状态后，红灯处于闪烁状态，且同时切断输出，以 200Hz 持续时间 200ms 的低频提示音表示。若此时绿灯亮起，表明超级电容正尝试重新启动，若绿灯不亮，则需要用户手动重置 超级电容模块。重置方法如下：
2. 用户可手动断开所有电源连接线，之后再逐个插入，超级电容即重新启动，若顺利通过故障检测， 则故障状态解除。
3. 用户可通过 CAN 发送重启指令，超级电容重新启动，若顺利通过故障检测，则故障状态解除。
4. 用户可通过 CAN 发送关断输出指令，之后再次发送启动输出指令，超级电容会尝试重新启动输出， 若未再次发生故障，正常运行一段时间后故障状态自动解除。

### 附加功能

- 监测裁判系统供电电压。若常低于某一值（约20V），则认为电池即将耗尽，蜂鸣器长鸣。用来提醒调试人员，防止出现调试代码未保存的情况。

# 电容组硬件

## 原理与设计比较

储能元件采用超级电容，耐压2.7V。电容组先并联再串联，增大耐压至29.15V，最终储能能力1931J。为了防止充电过程中由于电容体质不同，使得：有些节点还没充满时，另一些电容已经超过耐压的情况，使用均衡电路。

均衡电路分为主动均衡与被动均衡。

**被动均衡**一般通过电阻放电的方式，对电压较高的电容进行放电，以热形式释放电量。

此方案的优点是电路结构非常简单，研发成本也很低。先前可使用TL431电压基准模块进行简单搭建。后续随着BW6101超级电容保护芯片的推出，此方案更加简单廉价。

缺点较为显著，首先均衡时不存在电能转移，所有均衡的能量都通过电阻发热释放，理论上的均衡效率为0%。同时转移时会产生大量的热能，若不加处理，可能会烧毁电路。

**主动均衡**是一种复杂的均衡技术，在充电和放电循环期间，使得电容单元内的电荷得到重新分配，从而缩短充电时间，延长放电使用时间。如：

1. Flying Capacitor

   此电路实现了电荷泵，通过不断地控制开关，将电压较高的单元内电荷转移至中间电容器中，再转移至电压较低的单元。

   

   此方案的优势是具备主动均衡能力，理论上电容组可串联不同容量的超级电容。

   缺点是均衡速度不够快，可能需要添加被动均衡电路防止大电流充电时均衡失败。同时，额外的MOS管驱动方案也对设计者提出了较高的要求，额外的器件也带来了更多的成本。效率上，相比被动均衡，部分能量得到了重复利用，但是驱动MOS管开关也会带来额外损耗，建议把控好启动均衡的阈值电压，在电压较低时不启动MOS管驱动，节省能量。
2. 电感转换器

   使用电压较高的单元给电感充能，然后电感给电压较低的单元充电。

   

   此方案类似变形的buck电路，通过电感和电容组成的dcdc电路转移能量。其理论上能产生更大的均衡电流，但仍然存在上一个方案的一些缺点。同时如需更大的均衡电流，需要选择更大体积的功率电感，同样也会使总体体积增大。
3. 反激式电感转换器

   使用变压器实现所有电容一起给一个或多个电压较低的电容充电，通过定期控制MOS管的开关，实现电感两侧横恒电压控制，进而逐渐均衡各电容单元电压。

   

   此方案优缺点与上述两个方案类似，但还存在一个额外的缺点，即很难找到这种多绕组的变压器成品，在设计时可能需要自行制作变压器，较为繁琐，对设计制作要求较高。

总而言之，主动均衡能达到比被动均衡更高的能量利用率，然而在体积、效率、成本、可靠性上难以平衡。因此，进行部分尝试后，我们最终在本赛季放弃了主动均衡，使用基于电阻泄放的被动均衡结构制作了电容组阵列。

## 原理图

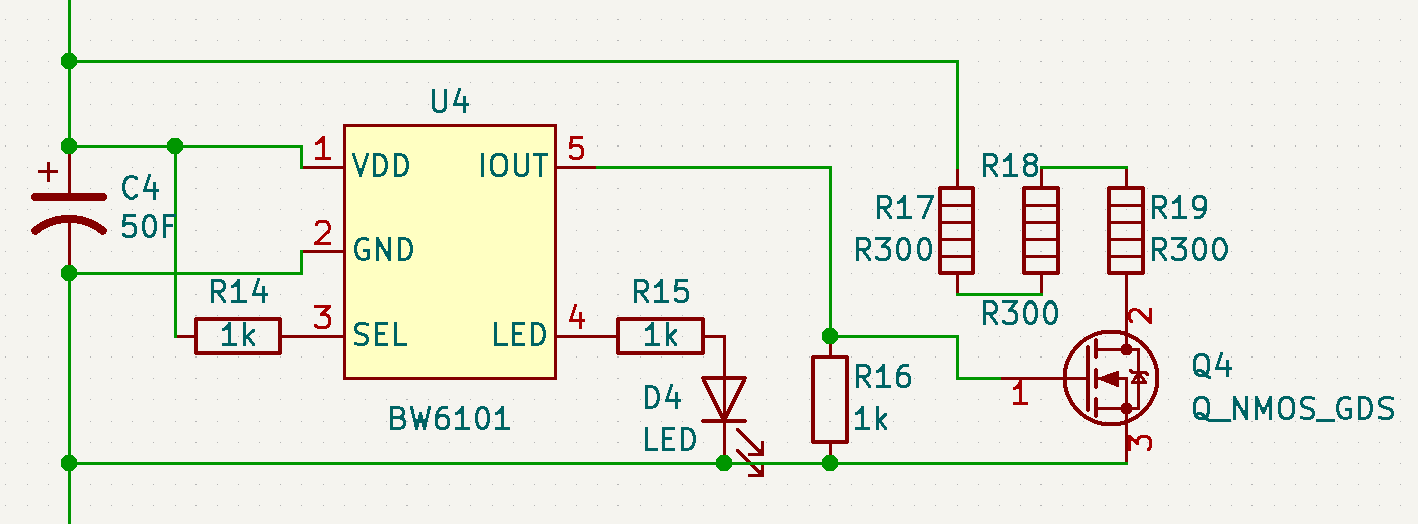
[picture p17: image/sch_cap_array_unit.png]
sch_cap_array_unit


图为一个电容单元。设计的电容组中共有11个该单元串联。

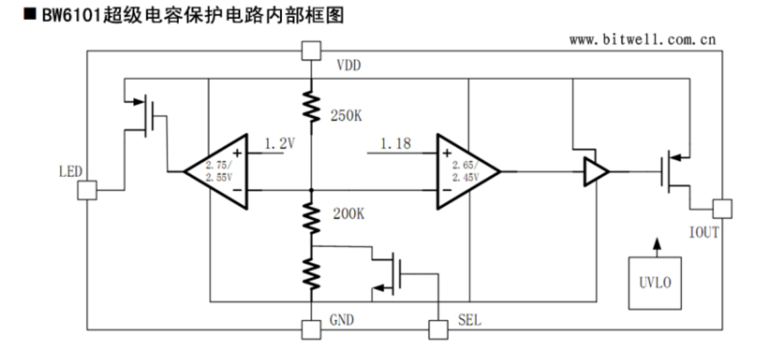
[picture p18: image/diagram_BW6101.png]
diagram_BW6101


控制芯片为BW6101，该芯片在电容电压(VDD - GND)大于2.65V时，控制NMOS对GND导通，此时电流通过泄流电阻泄放，从而消耗电容中过多的能量。

此处使用3个电阻串联，而不是并联的原因是难以找到1Ohm左右的大功率电阻，此处使用的0.3Ohm电阻为电流采样电阻，功率较大（3W），能够承受更大的泄放电流。

由于电容组需要经过裁判系统超级电容管理模块，而管理模块额定电流为15A，为了裁判系统的稳定工作及排除电流超限带来的偷功率嫌疑，我们将电容组的充放电电流限制为14.5A。在此约束下，电压越高，电容放电功率越大。我们选择11个2.7V 50F的超级电容串联，能够带来更高的最大电压，从而最大化输出功率，但由于超级电容等效串联电阻的存在，这种方案会较大程度损失效率。同时，值得注意的是，BW6101在电容充电至2.65V时就已经开始均衡，为减少均衡损耗，提升系统综合稳定性，我们决定只将电容充电至2.65V。

实际使用过程中，为防止非硬件开发人员拆装及使用电容组时由于经验不足错误操作发生危险，我们在电容组的输入端加入一个大功率单向TVS，在严重过充时可烧毁短路，保护电容组，若电容组与数控超级电容控制模块的正负极接反，该设计可配合短路保护功能进行保护，防止对电容组进行反极性充电。同时我们还加入了一个LED灯，用来警告操作人员电容的带电情况。在RoboMaster2023的备赛中，我们发生了至少两次电容组极性接反的情况（XT30反着用力插也是可以插上的），均触发了过流保护，成功及时关断。提示灯也多次在拆装电容组时提示操作人员带电情况，对电容及时放电。我们在整个备赛期间未发生任何一起电容组过充、短路、起火等严重后果。

## PCB

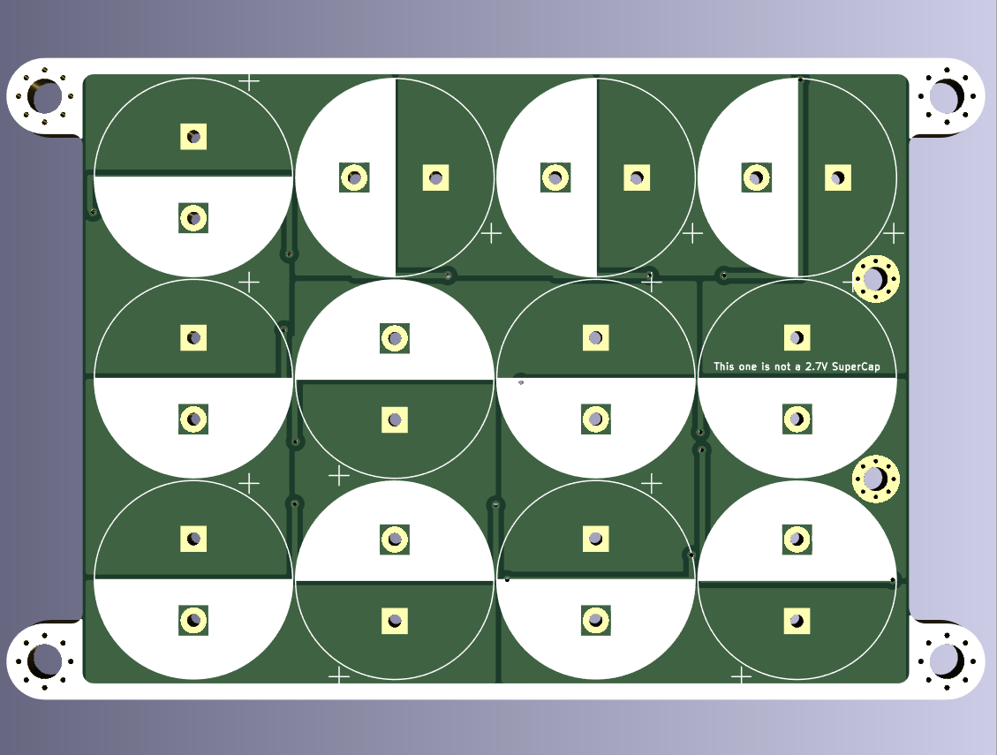
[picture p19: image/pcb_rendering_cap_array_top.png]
pcb_rendering_cap_array_top


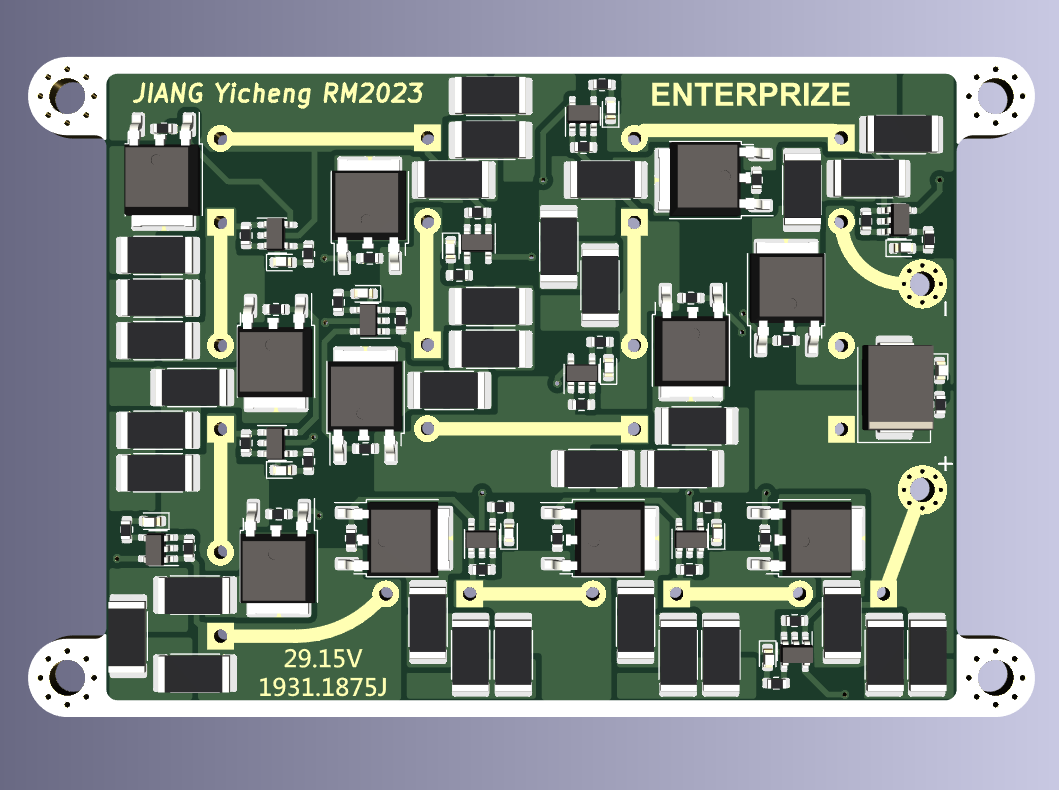
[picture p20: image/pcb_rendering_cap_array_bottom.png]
pcb_rendering_cap_array_bottom


*Layout 参考*

该模块layout较为极限，所有电容紧贴排列。为了加强散热，使用四层板。其中内层1、2与顶层铺铜相同，起导热作用。底层放置MOS与芯片等元件，并利用开窗导线减小电阻。过充测试时，使用2.5A电流长时间对电容组进行充电，电容组未出现严重过热情况，电容未出现过充情况。

## 实物

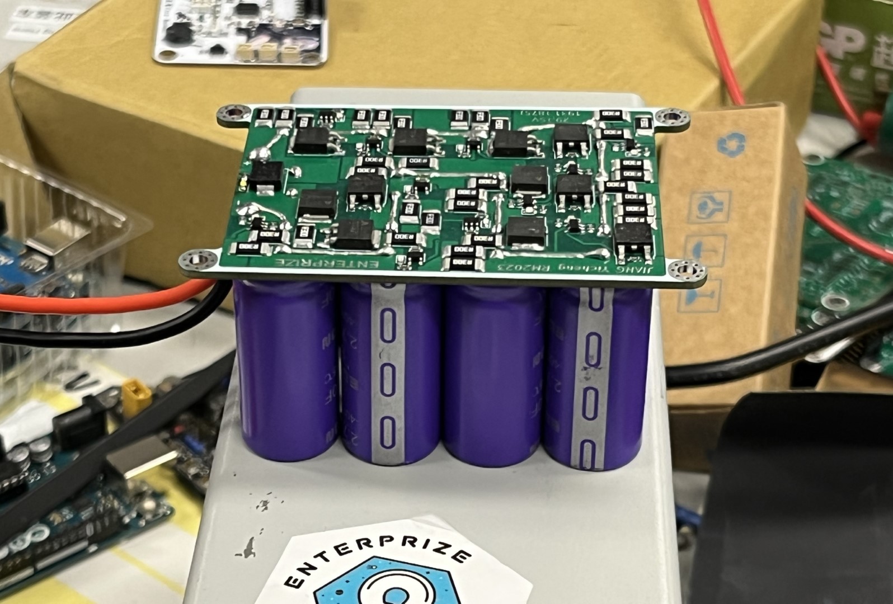
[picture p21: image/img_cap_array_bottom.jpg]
img_cap_array_bottom


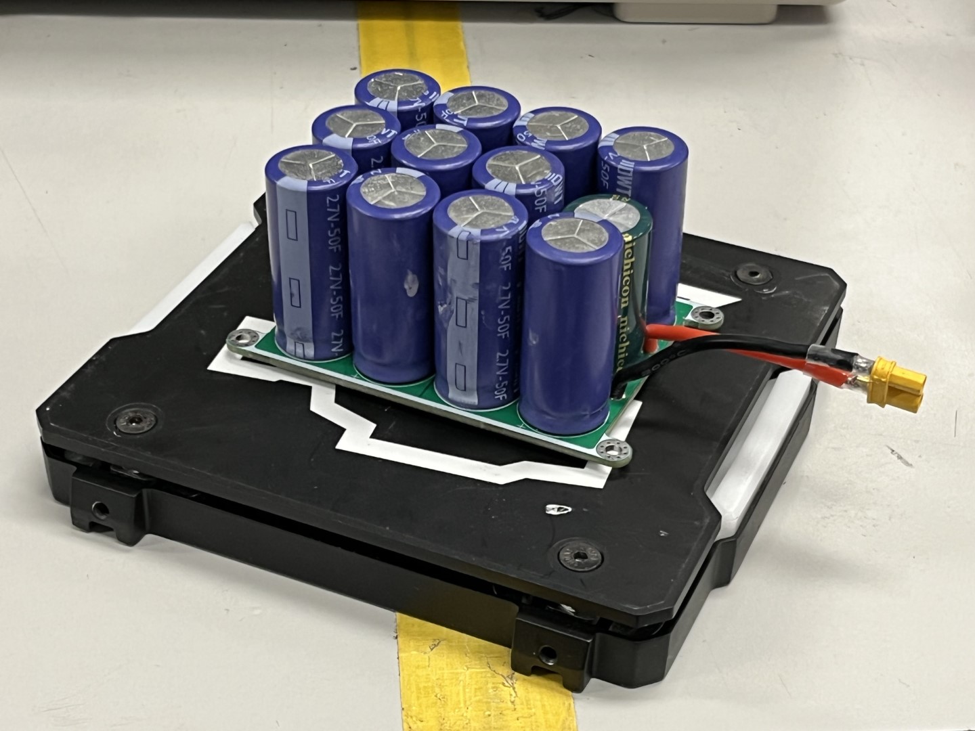
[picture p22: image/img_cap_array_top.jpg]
img_cap_array_top


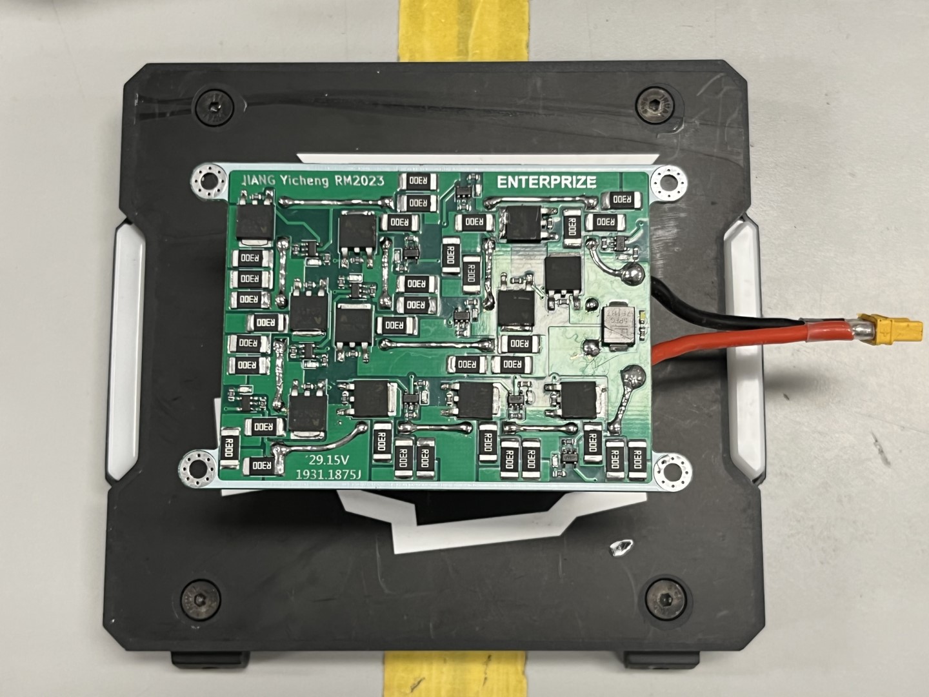
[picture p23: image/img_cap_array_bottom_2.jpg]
img_cap_array_bottom_2


超级电容组体积仅为60x76x45mm，在经费有限无法定制的情况下实现了较小的体积，机械设计更加自由。

# 总结

## 技术总结

本模块通过数控Buck-Boost电路，接受裁判系统或开发板的指令并反馈，来实现裁判系统输入功率闭环。闲时为电容组充电、有需求时为底盘放电，削峰填谷。升降压的拓扑在实现电机母线电压稳定的同时也使得电容组的能量利用率提高，且通过软件控制，既可以弥补硬件恒功率控制上的繁琐与复杂，也可以实现更灵活的功率控制与故障处理操作，甚至裁判系统能量缓冲闭环。

## 使用方式

### 硬件连线

功率线有三组：

- 左端有一根XT30公线，连接裁判系统电源模块Chassis接口
- 左端XT30母线，连接到其他底盘功率器件（如底盘电机等）
- 右端XT30公线，连接到超级电容组（经过CM01模块）

信号线

- MX1.25x4pin插座可以连接SWD调试线
- GH1.25x2pin插座连接CAN信号，与主板通信
- 预留了GH1.25x4pin IIC接口，可以连接OLED屏幕用作调试

### 通信协议

```c++
struct CapacitorStatus
{
    //本段结构体位于机器人控制代码与超级电容通信的Driver层中
    struct CapacitorRx
    {
        uint8_t errorCode;
        float chassisPower;
        uint16_t chassisPowerLimit;
        uint8_t capEnergy;
    } __attribute__((packed)) capacitorRx;

    struct CapacitorTx
    {
        uint8_t enableDCDC : 1;
        uint8_t systemRestart : 1;
        uint8_t resv0 : 6;
        uint16_t feedbackJudgePowerLimit;
        uint16_t feedbackJudgePowerBuffer;
        uint8_t resv1[3];
    } __attribute__((packed)) capacitorTx;

    bool isConnected;
};
```

## 测试结果

### 极限转换效率

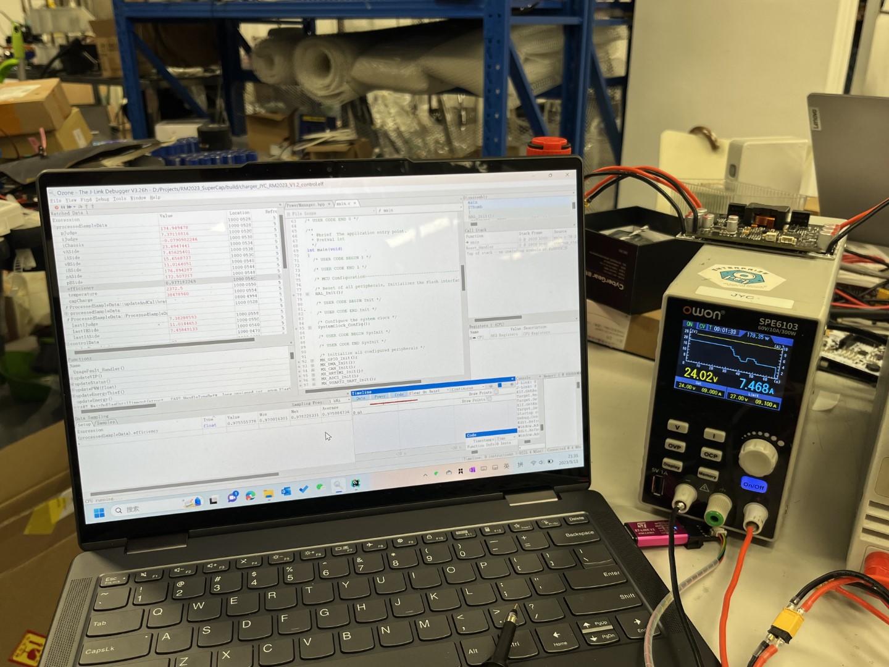
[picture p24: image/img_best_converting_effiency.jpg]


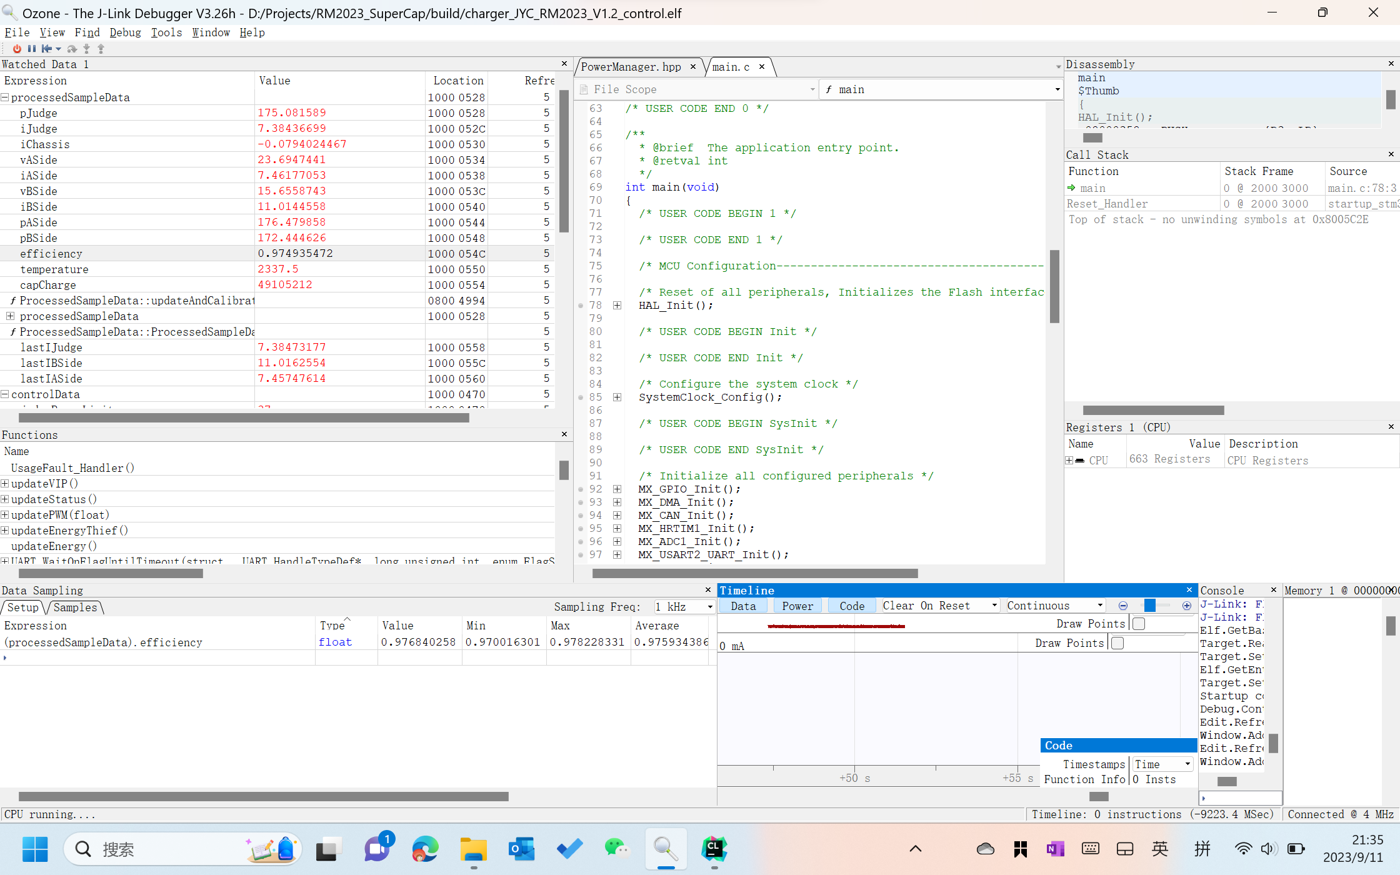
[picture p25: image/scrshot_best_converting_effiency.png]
scrshot_best_converting_effiency


*峰值效率0.978，一般效率约0.95*

### 输出纹波@5A

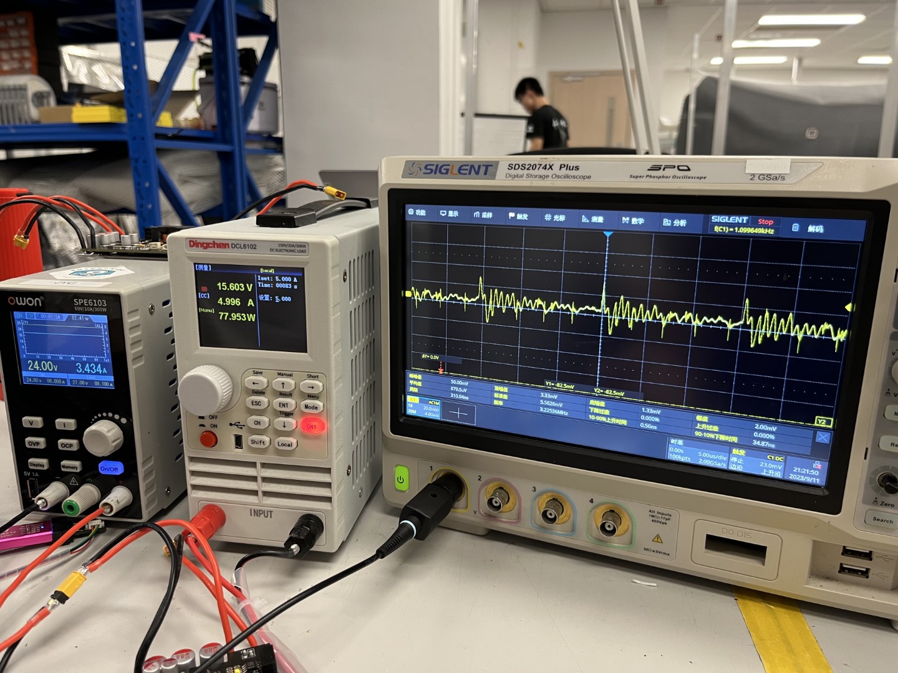
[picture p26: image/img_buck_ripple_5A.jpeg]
img_buck_ripple_5A


*Buck模式，占空比0.7：纹波25mV*

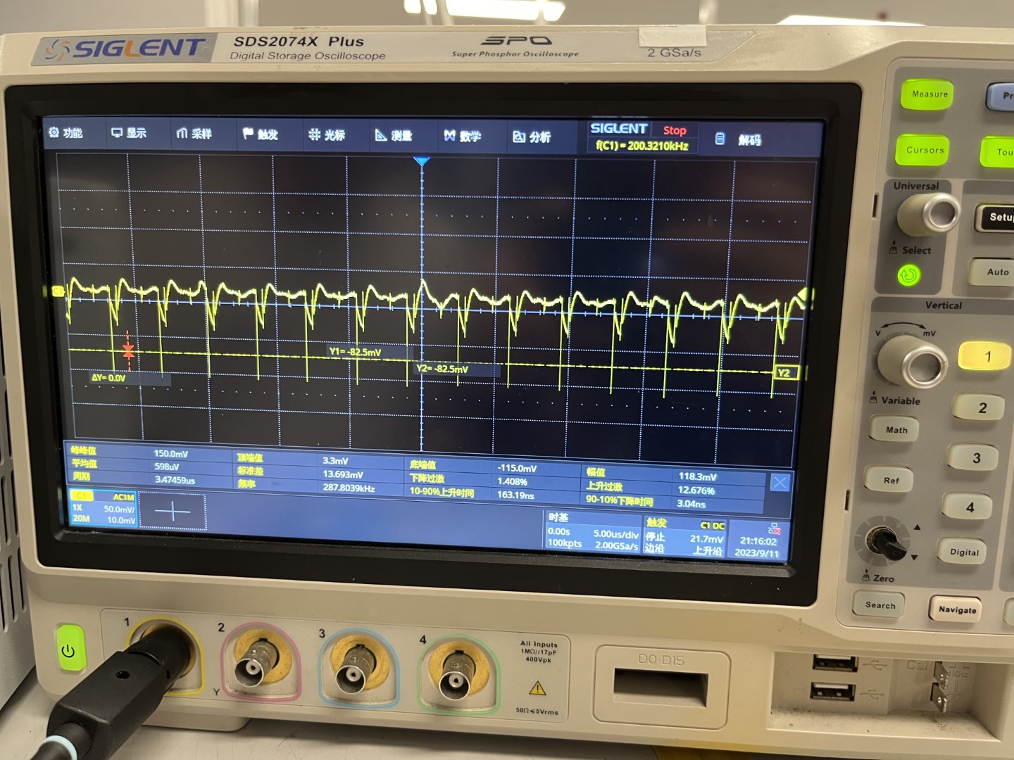
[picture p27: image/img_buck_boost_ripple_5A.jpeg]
img_buck_boost_ripple_5A


*Buck-Boost模式，“占空比”为1.0：纹波约50mV*

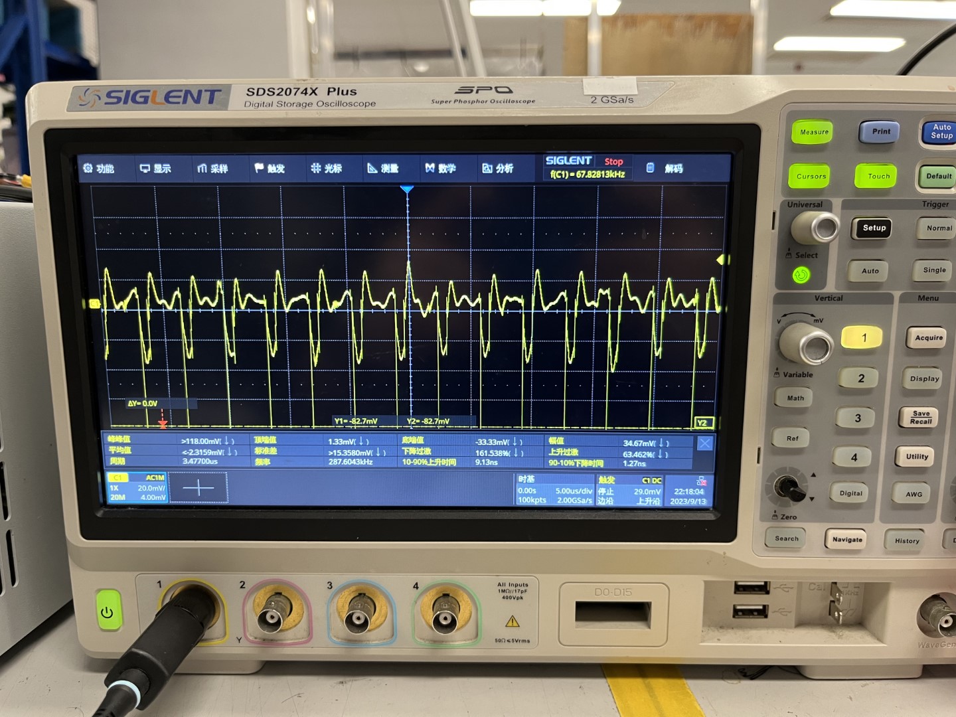
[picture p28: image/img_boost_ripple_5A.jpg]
img_boost_ripple_5A


*Boost模式，占空比0.75，纹波32mV*

## 发展方向

### 超级电容控制器

对于该版本控制器，大负载测试中发热极小，无需较大的散热面积与两MOS管并联的设计，体积可以很大程度的缩小；同时，有部分元件可以缩减，比如电压跟随运放可以利用MCU(STM32F334)内部的运放，从而减小复杂度、成本与体积。

为方便控制与简化硬件设计，本方案选用了理论效果不算出众的软件平均电流控制模式。可考虑略微修改硬件，以使用基于硬件比较器触发的电感峰值电流控制，实现逐周期电流闭环，提升系统响应。同时，本方案使用FPWM（强制脉宽调制）模式进行控制，这种控制方案在低负载情况下电感上会有电流反向流动，同时开关频率恒定，轻载时效率较低，瞬态响应一般。可考虑采用COT（恒定导通时间）提升瞬态响应，考虑加入PFM（脉冲频率调制）提升轻载效率。

考虑到软件控制电压电流等闭环确实存在不稳定因素，今后也考虑使用一些内置ARM内核和硬件反馈环路的数字电源控制芯片。它们一方面使用硬件环路补偿、开关控制等，更加稳定、集成度高，另一方面也可以烧入代码，实现功率、能量闭环、裁判系统通讯、底盘控制等操作，灵活性高。

而运用其他DC-DC拓扑的控制器也可以研究，例如Flyback（反驰）拓扑升降压，理论上可以用更少的MOS管与更简单的驱动电路（仅低位驱动）来实现给电容充电放电等功能。

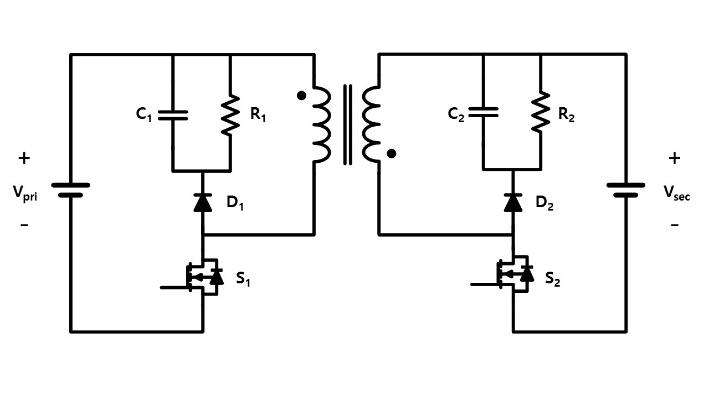
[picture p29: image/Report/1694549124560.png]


## 后记与致谢

大约于2018年，大连交通大学TOE战队，桂林电子科技大学Evolution战队与香港科技大学ENTERPRIZE战队等便相继开源了各具特色的超级电容方案，推动了RoboMaster中各队对突破底盘功率限制的技术发展，也使得这一项目进入规则中。在此对各位拓荒的前辈们致以感谢。

2021年，大连理工大学凌_BUG战队首次开源了基于Buck-Boost的超级电容控制器。这种架构作为目前阶段（RM2023）中超级电容毋庸置疑的最优解，对本项目有极大的参考价值。

从时间线上看来，其实我们在2018年之后就拥有了稳定可用的超级电容，并且多年来一直实装，效果很好。然而经过漫长的四年，一方面老超级电容确实存在资料较少、难以传承的问题，导致维护困难（甚至老的设计上使用的元件都找不到了）；另一方面，大连理工大学凌_BUG战队首发的Buck-Boost架构双向超级电容比起我们的老电容（电源 $\Rightarrow$ 恒功率充电模块 $\Rightarrow$ 超级电容 $\Rightarrow$ 恒压放电模块 $\Leftrightarrow$ 底盘电机）在各方面上都有着极大的提升。因而我们开启了这个新项目。

在超级电容的设计过程中，其他队伍的开源给予了我们莫大的帮助，在此感谢大连理工大学凌_BUG战队、西交利物浦GMaster战队与仲恺奇点战队等极为优秀的开源，以及在网上和七黄、光速翼等大佬的交流。也非常感谢嘉立创的低价打板与SMT服务（板子上元件很多，还好抽到了贴片券，节省了大量人力）。

2023赛季已经进入尾声，愿ENTERPRIZE战队在RM2024继续前进，再创新高！

最后，喊出那句口号，**初心高于胜负!**

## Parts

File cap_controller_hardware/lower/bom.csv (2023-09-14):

Designator | Footprint | Quantity | Value | LCSC Part #
C1, C2, C3, C7, C8, C9 | CP_Elec_10x14.3 | 6 | 220uF
C10, C11, C12, C13, C14, C15, C16, C4 | 1210 | 8 | 10uF
D1, D2, D3, D4 | D_SMF | 4 | SMF10A
D5, D6 | D_SMC | 2 | SMCJ33A
F1, F2 | Fuseholder_Littelfuse_Nano2_157x | 2 | Fuse
H1, H10, H2, H3, H4, H9 | Pad_3 | 6 | MountingHole_Pad
J3 | PinHeader_2x03_P2.54mm_Vertical_SMD | 1 | Conn_02x03_Odd_Even
J4, J5, J6, J7, J8, J9 | PinHeader_2x02_P2.54mm_Vertical_SMD | 6 | Conn_02x02_Odd_Even
Q1, Q2, Q3, Q4, Q5, Q6, Q7, Q8 | TDSON-8-1 | 8 | BSC070N10NS3G
R1, R2, R3 | 2512 | 3 | 4mR
R4, R5, R6, R7 | 0603 | 4 | 10k
TH1 | 1206 | 1 | Thermistor
U1 | PQ2617BHA | 1 | 10uH

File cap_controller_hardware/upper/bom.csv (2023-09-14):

Designator | Footprint | Quantity | Value | LCSC Part #
BZ1 | MLT-9032 | 1 | Buzzer
C1, C102, C103, C104, C105, C106, C107, C16, C17, C18, C2, C21, C22, C23, C24, C25, C29, C30, C31, C35, C37, C40, C41, C42, C43, C45, C47, C49, C50, C51, C52, C54, C55, C58, C59, C62, C67, C70, C71, C72, C74, C76, C77, C78, C79, C81, C83, C87, C88, C91, C92, C94, C95, C97, C99 | 0603 | 55 | 100n
C10, C5, C53, C57, C6, C7, C8, C9 | 1206 | 8 | 10u
C100, C101, C14, C15, C19, C20, C32, C33, C36, C39, C44, C56, C63, C64, C66, C68, C69, C75, C80, C82, C84, C85, C86, C89, C90, C93, C96, C98 | 0603 | 28 | 10u
C12 | CP_Radial_D6.3mm_P2.50mm | 1 | 680u
C13, C28, C48, C65, C73 | CP_EIA-3216-18_Kemet-A | 5 | 47u
C26 | CP_Radial_D6.3mm_P2.50mm | 1 | 220u
C3, C4 | 0603 | 2 | 100p
C34, C46 | 0603 | 2 | 10n
C38 | 0603 | 1 | 20p
C60, C61 | CP_Radial_D6.3mm_P2.50mm | 2 | 47u
D1, D10, D11, D18, D2, D21, D8, D9 | D_SMF | 8 | K34
D12, D13, D14, D15, D17, D23, D25, D27, D4, D5, D6 | 0603 | 11 | LED
D16, D19, D20, D22 | D_SMF | 4 | SMF10A
D3 | D_SMF | 1 | SMCJ28A
D7 | D_SMF | 1 | SMF5V0A
F1 | 1210 | 1 | Polyfuse
F2 | 1206 | 1 | Polyfuse
J1, J10, J12, J2, J4, J6 | conn_2x02_2.54 | 6 | Conn_02x02_Odd_Even
J11, J8 | JST_GH_BM03B-GHS-TBT_1x03-1MP_P1.25mm_Vertical | 2 | Conn_UART
J13 | JST_GH_BM02B-GHS-TBT_1x02-1MP_P1.25mm_Vertical | 1 | Conn_CAN
J3 | conn_2x03_2.54 | 1 | Conn_02x03_Odd_Even
J5 | JST_GH_BM04B-GHS-TBT_1x04-1MP_P1.25mm_Vertical | 1 | Conn_OLED
J9 | Molex_PicoBlade_53261-0471_1x04-1MP_P1.25mm_Horizontal | 1 | Conn_SWD
L1, L2 | L_Bourns-SRN4018 | 2 | 6R8
L3, L4, L5 | 0603 | 3 | L_Ferrite
Q1 | SOT-23 | 1 | AO3400A
R1, R23, R7, R8 | 0603 | 4 | 100k 25ppm
R10, R11, R16 | 0603 | 3 | 200r
R12 | 0603 | 1 | 118k
R13, R15, R28, R29, R3, R35, R4, R41, R42, R51, R58 | 0603 | 11 | 10k
R14 | 0603 | 1 | 53.6k
R17, R19, R34, R36, R37, R46, R47 | 0603 | 7 | 120r
R18, R2 | 0603 | 2 | 10k 25ppm
R20, R25, R32, R33, R44, R45, R5, R57, R6, R64, R65 | 0603 | 11 | 33r
R21, R22, R53, R63 | 1206 | 4 | 3.3r
R24, R30, R31, R39, R43, R50, R52, R55, R61, R62 | 0603 | 10 | 1k
R26 | 0603 | 1 | 100k
R27 | 0603 | 1 | 51k
R38, R40 | 0603 | 2 | 2.2k
R48, R49 | 1206 | 2 | 68r
R54, R56, R59, R60, R66, R67 | 0603 | 6 | 100r 25ppm
R9 | 0603 | 1 | 5k
U1 | SOT-23 | 1 | REF3033
U11 | SOIC-8_3.9x4.9mm_P1.27mm | 1 | TJA1042T-3
U12, U13 | SOT-23-5 | 2 | RS3236
U14, U15 | BxxxxS-1W | 2 | ISO_DC
U16, U17 | SOIC-8_3.9x4.9mm_P1.27mm | 2 | UCC27211D
U19, U7, U8 | SOT-363_SC-70-6 | 3 | INA186
U2 | LQFP-64_10x10mm_P0.5mm | 1 | STM32F334R8Tx
U3, U4 | SOT-23-6 | 2 | RY8411
U5, U9 | SOIC-8_3.9x4.9mm_P1.27mm | 2 | GS8332-SR
Y1 | Resonator_SMD_Murata_CSTxExxV-3Pin_3.0x1.1mm | 1 | 8MHz

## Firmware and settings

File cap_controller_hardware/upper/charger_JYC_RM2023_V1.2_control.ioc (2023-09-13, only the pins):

Mcu.UserName=STM32F334R8Tx
PA0.Signal=ADC1_IN1
PA1.Signal=ADC1_IN2
PA10.Signal=HRTIM1_CHB1
PA11.Signal=HRTIM1_CHB2
PA13.Signal=SYS_JTMS-SWDIO
PA14.Signal=SYS_JTCK-SWCLK
PA2.Signal=ADC1_IN3
PA8.Signal=HRTIM1_CHA1
PA9.Signal=HRTIM1_CHA2
PB0.Signal=TIM1_CH2N
PB10.Signal=HRTIM1_FLT3
PB11.Signal=HRTIM1_FLT4
PB14.Signal=S_TIM15_CH1
PB15.Signal=S_TIM15_CH2
PB3.Signal=USART2_TX
PB4.Signal=USART2_RX
PB8.Signal=CAN_RX
PB9.Signal=CAN_TX
PC1.Signal=ADCx_IN7
PC2.Signal=ADCx_IN8
PC3.Signal=ADCx_IN9
PC6.Signal=S_TIM3_CH1
PC7.Signal=S_TIM3_CH2
PC8.Signal=S_TIM3_CH3
PC9.Signal=S_TIM3_CH4

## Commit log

2023-09-14 Generating gerber and bom
    [bom.csv, charger_JYC_RM2023_V1.2_control.kicad_pcb, charger_JYC_RM2023_V1.2_control.kicad_sch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]
2023-09-14 Adding cap array hardware
    [capArray_JYC_RM2023_V0.2.kicad_pcb, capArray_JYC_RM2023_V0.2.kicad_sch]
